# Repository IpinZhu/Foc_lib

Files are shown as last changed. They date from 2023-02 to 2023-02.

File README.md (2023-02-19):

## 重启Foc项目(Great FOC Restart Project)

### 1.概论和目标

基于STM32系列芯片的HAL库Foc代码库，和配套硬件电路

1.采用基本的Foc算法,支持开环和闭环，提供标准API接口

2.自动PID校准功能（待定）

3.支持有感电机和无感电机

4.引入龙伯格观测器，实现无感滤波

5.Rtos程序，可加入用户自定APP

6.宽电压输入范围和输出大电流



### 2.硬件

1.使用DRV8301作为三路逆变器的控制芯片，将功率模块和控制模块区分成上下半区部分。

2.主控采用STM32F405RGT6

3.提供一个外部SPI,一个CAN总线和一个复用的TypeC口，可同时将设备进行串口通信和作为USB设备使用

##### DRV8301

自带一个TPS54160Buck芯片，可以对6-60v输入进行降压处理，由于实际使用不超过25V，因此选取6-35V的输入范围，输出5V电压

### 3.软件

##### 1.foc.c和foc.h

主要由基本foc算法变换，参照st电机库，使用Q1.15形式（注.无法使用Q1.32格式，计算时会溢出）

##### SVPWM：

##### 定时器配置

分频系数为1-1=0

计数模式为中心计数模式，作用频率为10k，为168M/10K/2

RCR设置为1

### 4.RTOS

主任务

屏幕显示任务

### 5.上位机

懒得写。。。。。。

 Foc_lib

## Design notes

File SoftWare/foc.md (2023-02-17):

## 重启Foc项目(Great FOC Restart Project)

### 1.概论

基于STM32系列芯片的HAL库Foc代码库，适用于几乎所有的STM32芯片

1.采用基本的Foc算法,支持开环和闭环，提供标准API接口

2.自动PID校准功能（待定）

3.支持有感电机和无感电机

4.引入龙伯格观测器，实现无感滤波

5.Rtos程序，可加入用户自定APP



### 2.硬件

使用DRV8301作为三路逆变器的控制芯片，将功率模块和控制模块区分成上下板部分

主控采用F405RGT6

##### DRV8301

自带一个TPS54160Buck芯片，可以对6-60v输入进行降压处理，由于实际使用不超过25V，因此选取6-35V的输入范围，输出5V电压



### 3.软件

##### 1.foc.c和foc.h

主要由基本foc算法变换，参照st电机库，使用Q1.15形式（注.无法使用Q1.32格式，计算时会溢出）



使用到的结构体：

```c
typedef struct
{
    int16_t alpha;
    int16_t beta;
} alphabeta_t;

typedef struct
{
    int16_t a;
    int16_t b;
} ab_t;

typedef struct
{
    int16_t q;
    int16_t d;
} qd_t;

typedef struct
{
    int16_t hCos;
    int16_t hSin;
} Trig_Components;
```

##### 2.svpwm.c和svpwm.h

##### 七段式定时器控制：







分频系数为1-1=0

计数模式为中心计数模式，作用频率为10k，为168M/10K/2

RCR设置为1

### 4.RTOS

主任务

屏幕显示任务

### 5.上位机

懒得写。。。。。。

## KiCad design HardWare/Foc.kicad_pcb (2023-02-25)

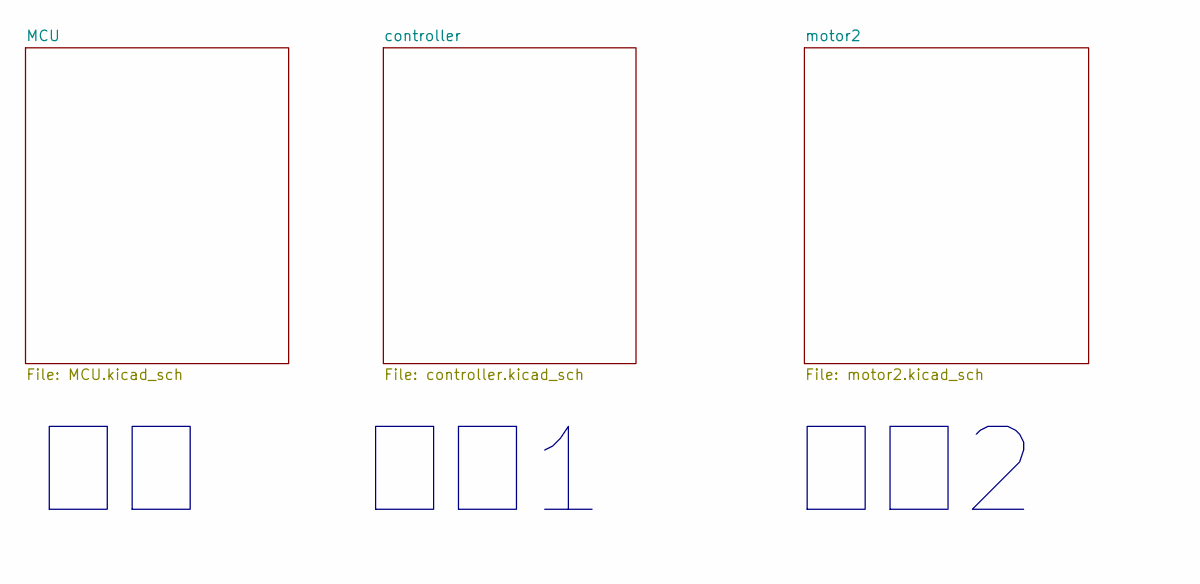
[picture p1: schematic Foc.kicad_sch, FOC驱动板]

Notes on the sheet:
电机2
电机1

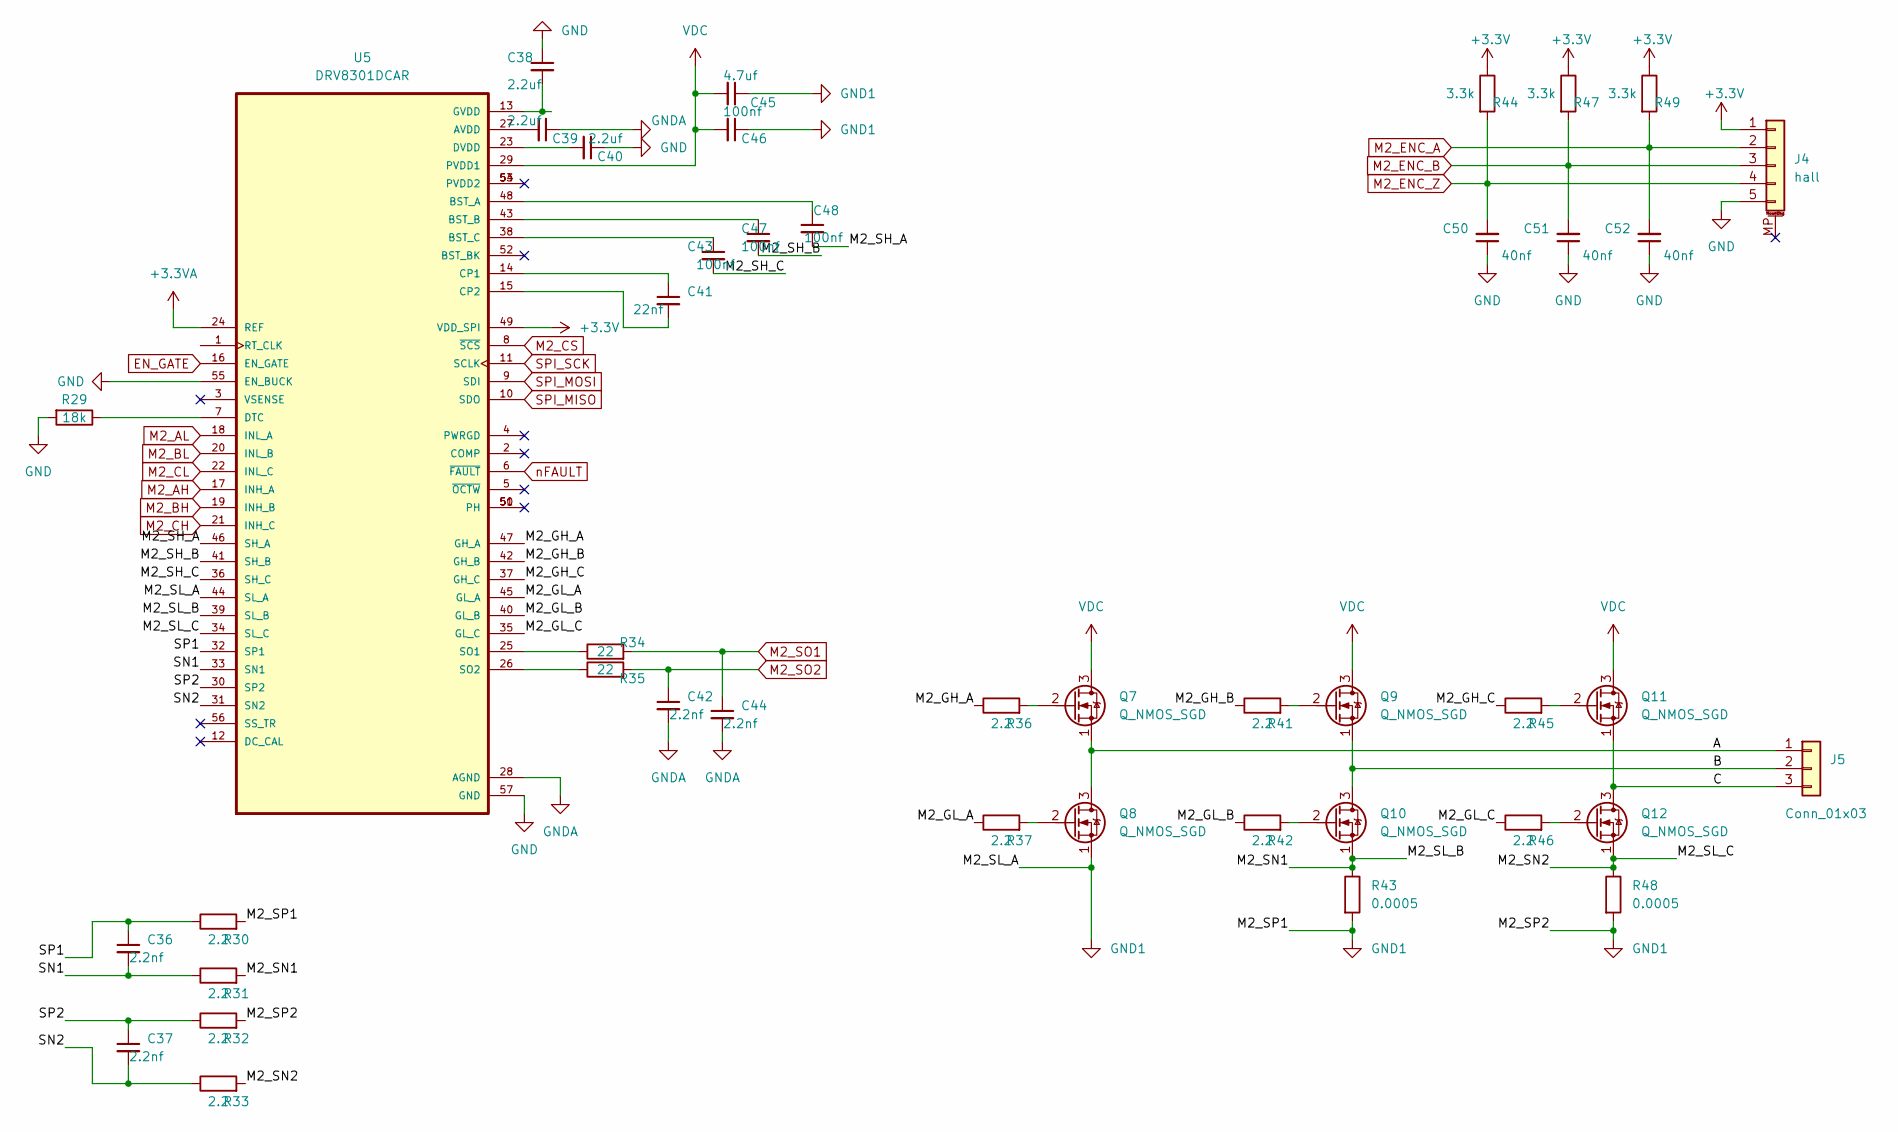
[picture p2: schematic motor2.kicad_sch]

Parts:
C36, C37, C42, C44: 2.2nf; C_0603_1608Metric
C38, C39, C40: 2.2uf; C_0603_1608Metric
C41: 22nf; C_0603_1608Metric
C43, C46, C47, C48: 100nf; C_0603_1608Metric
C45: 4.7uf; C_0603_1608Metric
C50, C51, C52: 40nf; C_0603_1608Metric
J4: hall; M1010RS-05P
J5: Conn_01x03; MR30-M
Q7, Q8, Q9, Q10, Q11, Q12: Q_NMOS_SGD; VSONP-8-1EP_5x6_P1.27mm
R29: 18k; R_0603_1608Metric
R30, R31, R32, R33, R36, R37, R41, R42, R45, R46: 2.2; R_0603_1608Metric
R34, R35: 22; R_0603_1608Metric
R43, R48: 0.0005; R_2512_6332Metric
R44, R47, R49: 3.3k; R_0603_1608Metric
U5: DRV8301DCAR; HTSSOP-56-1EP_6.1x14mm_P0.5mm_EP3.61x6.35mm; PARTREV F

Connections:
+3.3V: J4.1, R44.1, R47.1, R49.1, U5.49 (VDD_SPI); also elsewhere on the board
+3.3VA: U5.24 (REF); also elsewhere on the board
/motor2/A: J5.1, Q7.1 (S), Q8.3 (D)
/motor2/B: J5.2, Q9.1 (S), Q10.3 (D)
/motor2/C: J5.3, Q11.1 (S), Q12.3 (D)
/motor2/M2_GH_A: R36.1, U5.47 (GH_A)
/motor2/M2_GH_B: R41.1, U5.42 (GH_B)
/motor2/M2_GH_C: R45.1, U5.37 (GH_C)
/motor2/M2_GL_A: R37.1, U5.45 (GL_A)
/motor2/M2_GL_B: R42.1, U5.40 (GL_B)
/motor2/M2_GL_C: R46.1, U5.35 (GL_C)
/motor2/M2_SH_A: C48.2, U5.46 (SH_A)
/motor2/M2_SH_B: C47.2, U5.41 (SH_B)
/motor2/M2_SH_C: C43.2, U5.36 (SH_C)
/motor2/M2_SL_B: Q10.1 (S), R31.2, R43.1, U5.39 (SL_B)
/motor2/M2_SL_C: Q12.1 (S), R33.2, R48.1, U5.34 (SL_C)
/motor2/SN1: C36.2, R31.1, U5.33 (SN1)
/motor2/SN2: C37.2, R33.1, U5.31 (SN2)
/motor2/SP1: C36.1, R30.1, U5.32 (SP1)
/motor2/SP2: C37.1, R32.1, U5.30 (SP2)
EN_GATE: U5.16 (EN_GATE); also elsewhere on the board
GND: C38.1, C39.1, C40.1, C42.2, C44.2, C50.1, C51.1, C52.1, J4.5, R29.2, U5.28 (AGND), U5.55 (EN_BUCK), U5.57 (GND); also elsewhere on the board
GND1: C45.1, C46.1, Q8.1 (S), R30.2, R32.2, R43.2, R48.2, U5.44 (SL_A); also elsewhere on the board
M2_AH: U5.17 (INH_A); also elsewhere on the board
M2_AL: U5.18 (INL_A); also elsewhere on the board
M2_BH: U5.19 (INH_B); also elsewhere on the board
M2_BL: U5.20 (INL_B); also elsewhere on the board
M2_CH: U5.21 (INH_C); also elsewhere on the board
M2_CL: U5.22 (INL_C); also elsewhere on the board
M2_CS: U5.8 (~SCS); also elsewhere on the board
M2_ENC_A: C52.2, J4.2, R49.2; also elsewhere on the board
M2_ENC_B: C51.2, J4.3, R47.2; also elsewhere on the board
M2_ENC_Z: C50.2, J4.4, R44.2; also elsewhere on the board
M2_SO1: C44.1, R34.2; also elsewhere on the board
M2_SO2: C42.1, R35.2; also elsewhere on the board
unnamed: C38.2, U5.13 (GVDD)
unnamed: C39.2, U5.27 (AVDD)
unnamed: C40.2, U5.23 (DVDD)
unnamed: C41.1, U5.14 (CP1)
unnamed: C41.2, U5.15 (CP2)
unnamed: C43.1, U5.38 (BST_C)
unnamed: C47.1, U5.43 (BST_B)
unnamed: C48.1, U5.48 (BST_A)
unnamed: Q7.2 (G), R36.2
unnamed: Q8.2 (G), R37.2
unnamed: Q9.2 (G), R41.2
unnamed: Q10.2 (G), R42.2
unnamed: Q11.2 (G), R45.2
unnamed: Q12.2 (G), R46.2
unnamed: R29.1, U5.7 (DTC)
unnamed: R34.1, U5.25 (SO1)
unnamed: R35.1, U5.26 (SO2)
SPI_MISO: U5.10 (SDO); also elsewhere on the board
SPI_MOSI: U5.9 (SDI); also elsewhere on the board
SPI_SCK: U5.11 (SCLK); also elsewhere on the board
VDC: C45.2, C46.2, Q7.3 (D), Q9.3 (D), Q11.3 (D), U5.29 (PVDD1); also elsewhere on the board
nFAULT: U5.6 (~FAULT); also elsewhere on the board

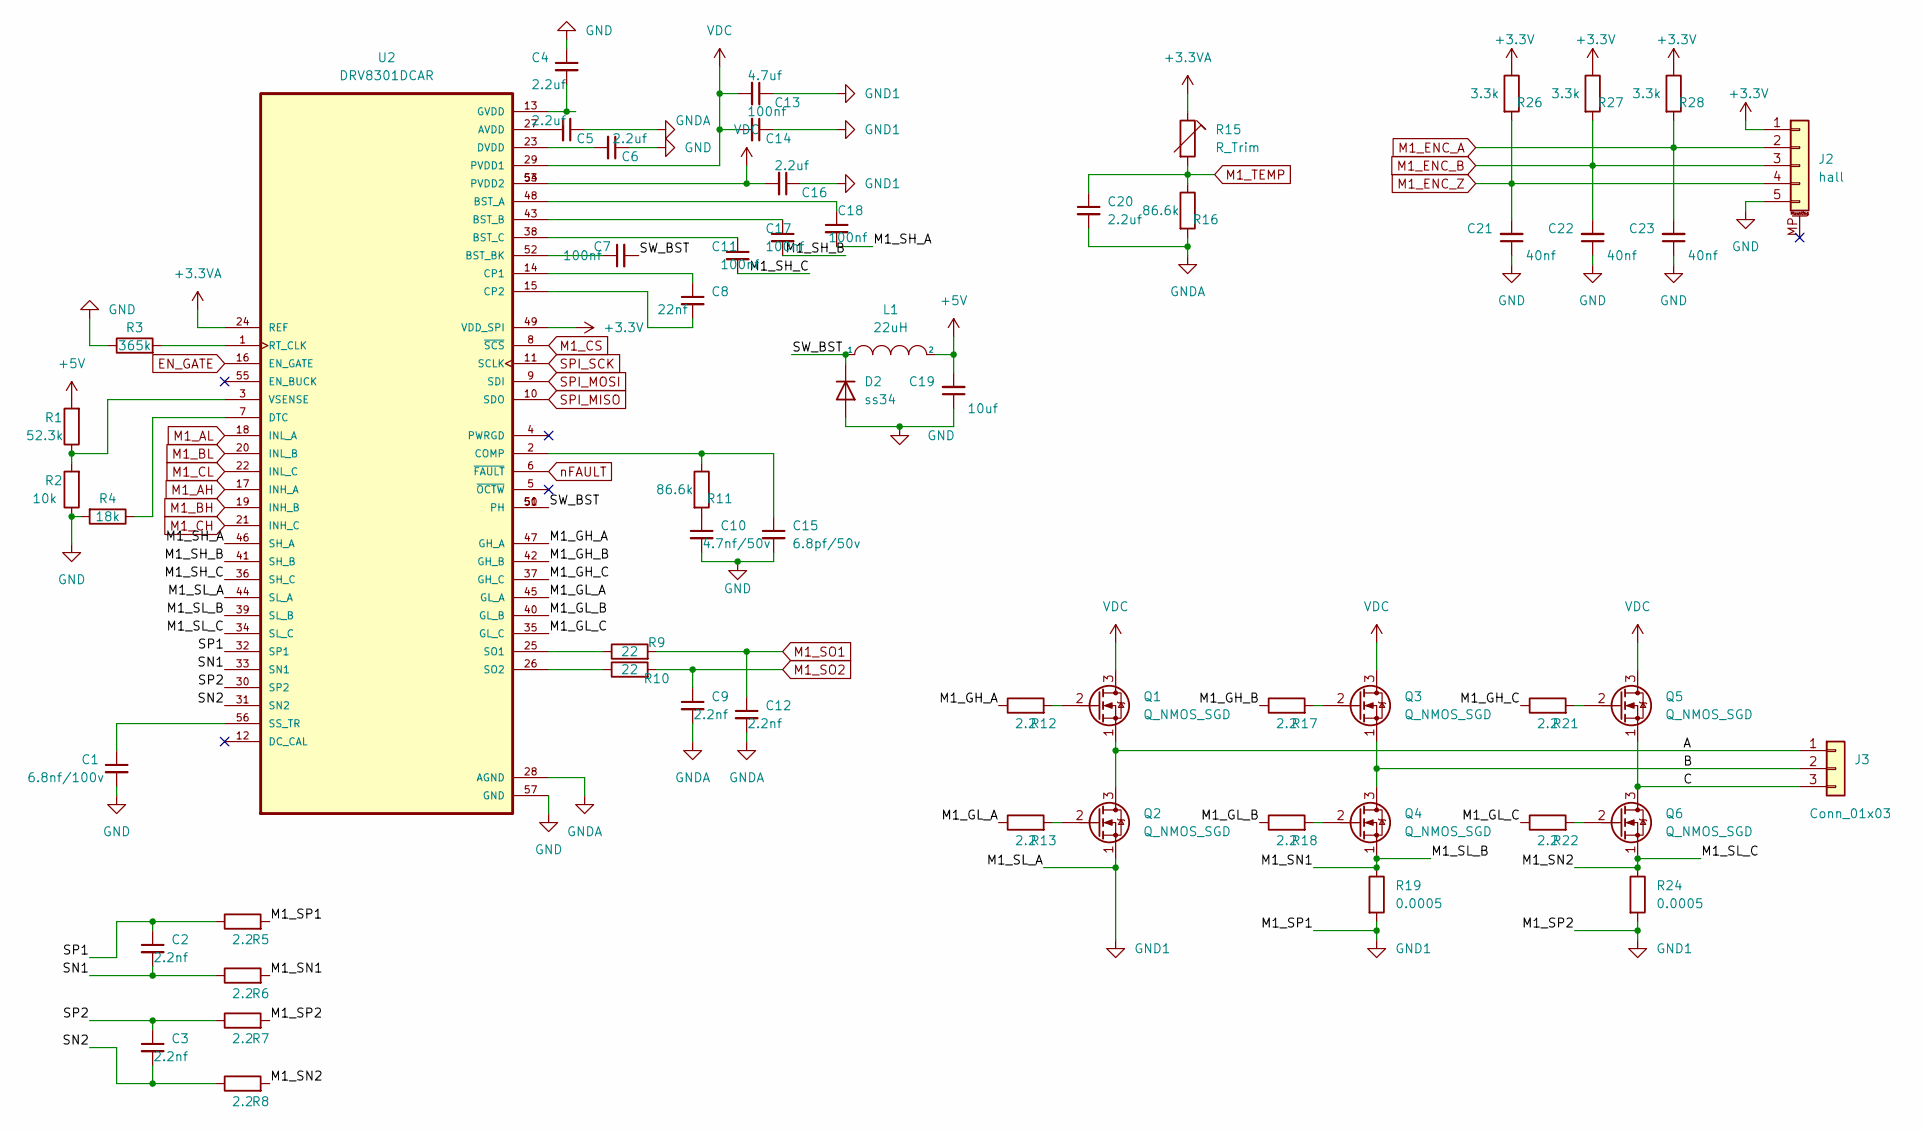
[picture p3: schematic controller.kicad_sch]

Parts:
C1: 6.8nf/100v; C_0603_1608Metric
C2, C3, C9, C12: 2.2nf; C_0603_1608Metric
C4, C5, C6, C16, C20: 2.2uf; C_0603_1608Metric
C7, C11, C14, C17, C18: 100nf; C_0603_1608Metric
C8: 22nf; C_0603_1608Metric
C10: 4.7nf/50v; C_0603_1608Metric
C13: 4.7uf; C_0603_1608Metric
C15: 6.8pf/50v; C_0603_1608Metric
C19: 10uf; C_1210_3225Metric
C21, C22, C23: 40nf; C_0603_1608Metric
D2: ss34; D_SMA
J2: hall; M1010RS-05P
J3: Conn_01x03; MR30-M
L1: 22uH; L_Abracon_ASPI-0630LR
Q1, Q2, Q3, Q4, Q5, Q6: Q_NMOS_SGD; VSONP-8-1EP_5x6_P1.27mm
R1: 52.3k; R_0603_1608Metric
R2: 10k; R_0603_1608Metric
R3: 365k; R_0603_1608Metric
R4: 18k; R_0603_1608Metric
R5, R6, R7, R8, R12, R13, R17, R18, R21, R22: 2.2; R_0603_1608Metric
R9, R10: 22; R_0603_1608Metric
R11, R16: 86.6k; R_0603_1608Metric
R15: R_Trim; R_0603_1608Metric
R19, R24: 0.0005; R_2512_6332Metric
R26, R27, R28: 3.3k; R_0603_1608Metric
U2: DRV8301DCAR; HTSSOP-56-1EP_6.1x14mm_P0.5mm_EP3.61x6.35mm; PARTREV F

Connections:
+3.3V: J2.1, R26.1, R27.1, R28.1, U2.49 (VDD_SPI); also elsewhere on the board
+3.3VA: R15.1, U2.24 (REF); also elsewhere on the board
+5V: C19.2, L1.2, R1.2; also elsewhere on the board
/controller/A: J3.1, Q1.1 (S), Q2.3 (D)
/controller/B: J3.2, Q3.1 (S), Q4.3 (D)
/controller/C: J3.3, Q5.1 (S), Q6.3 (D)
/controller/M1_GH_A: R12.1, U2.47 (GH_A)
/controller/M1_GH_B: R17.1, U2.42 (GH_B)
/controller/M1_GH_C: R21.1, U2.37 (GH_C)
/controller/M1_GL_A: R13.1, U2.45 (GL_A)
/controller/M1_GL_B: R18.1, U2.40 (GL_B)
/controller/M1_GL_C: R22.1, U2.35 (GL_C)
/controller/M1_SH_A: C18.2, U2.46 (SH_A)
/controller/M1_SH_B: C17.2, U2.41 (SH_B)
/controller/M1_SH_C: C11.2, U2.36 (SH_C)
/controller/M1_SL_B: Q4.1 (S), R6.2, R19.1, U2.39 (SL_B)
/controller/M1_SL_C: Q6.1 (S), R8.2, R24.1, U2.34 (SL_C)
/controller/SN1: C2.2, R6.1, U2.33 (SN1)
/controller/SN2: C3.2, R8.1, U2.31 (SN2)
/controller/SP1: C2.1, R5.1, U2.32 (SP1)
/controller/SP2: C3.1, R7.1, U2.30 (SP2)
/controller/SW_BST: C7.2, D2.2 (K), L1.1, U2.50 (PH), U2.51 (PH)
EN_GATE: U2.16 (EN_GATE); also elsewhere on the board
GND: C1.2, C4.1, C5.1, C6.1, C9.2, C10.2, C12.2, C15.2, C19.1, C20.2, C21.1, C22.1, C23.1, D2.1 (A), J2.5, R2.1, R3.1, R4.2, R16.2, U2.28 (AGND), U2.57 (GND); also elsewhere on the board
GND1: C13.1, C14.1, C16.1, Q2.1 (S), R5.2, R7.2, R19.2, R24.2, U2.44 (SL_A); also elsewhere on the board
M1_AH: U2.17 (INH_A); also elsewhere on the board
M1_AL: U2.18 (INL_A); also elsewhere on the board
M1_BH: U2.19 (INH_B); also elsewhere on the board
M1_BL: U2.20 (INL_B); also elsewhere on the board
M1_CH: U2.21 (INH_C); also elsewhere on the board
M1_CL: U2.22 (INL_C); also elsewhere on the board
M1_CS: U2.8 (~SCS); also elsewhere on the board
M1_ENC_A: C23.2, J2.2, R28.2; also elsewhere on the board
M1_ENC_B: C22.2, J2.3, R27.2; also elsewhere on the board
M1_ENC_Z: C21.2, J2.4, R26.2; also elsewhere on the board
M1_SO1: C12.1, R9.2; also elsewhere on the board
M1_SO2: C9.1, R10.2; also elsewhere on the board
M1_TEMP: C20.1, R15.2, R16.1; also elsewhere on the board
unnamed: C1.1, U2.56 (SS_TR)
unnamed: C4.2, U2.13 (GVDD)
unnamed: C5.2, U2.27 (AVDD)
unnamed: C6.2, U2.23 (DVDD)
unnamed: C7.1, U2.52 (BST_BK)
unnamed: C8.1, U2.14 (CP1)
unnamed: C8.2, U2.15 (CP2)
unnamed: C10.1, R11.2
unnamed: C11.1, U2.38 (BST_C)
unnamed: C15.1, R11.1, U2.2 (COMP)
unnamed: C17.1, U2.43 (BST_B)
unnamed: C18.1, U2.48 (BST_A)
unnamed: Q1.2 (G), R12.2
unnamed: Q2.2 (G), R13.2
unnamed: Q3.2 (G), R17.2
unnamed: Q4.2 (G), R18.2
unnamed: Q5.2 (G), R21.2
unnamed: Q6.2 (G), R22.2
unnamed: R1.1, R2.2, U2.3 (VSENSE)
unnamed: R3.2, U2.1 (RT_CLK)
unnamed: R4.1, U2.7 (DTC)
unnamed: R9.1, U2.25 (SO1)
unnamed: R10.1, U2.26 (SO2)
SPI_MISO: U2.10 (SDO); also elsewhere on the board
SPI_MOSI: U2.9 (SDI); also elsewhere on the board
SPI_SCK: U2.11 (SCLK); also elsewhere on the board
VDC: C13.2, C14.2, C16.2, Q1.3 (D), Q3.3 (D), Q5.3 (D), U2.29 (PVDD1), U2.53 (PVDD2), U2.54 (PVDD2); also elsewhere on the board
nFAULT: U2.6 (~FAULT); also elsewhere on the board

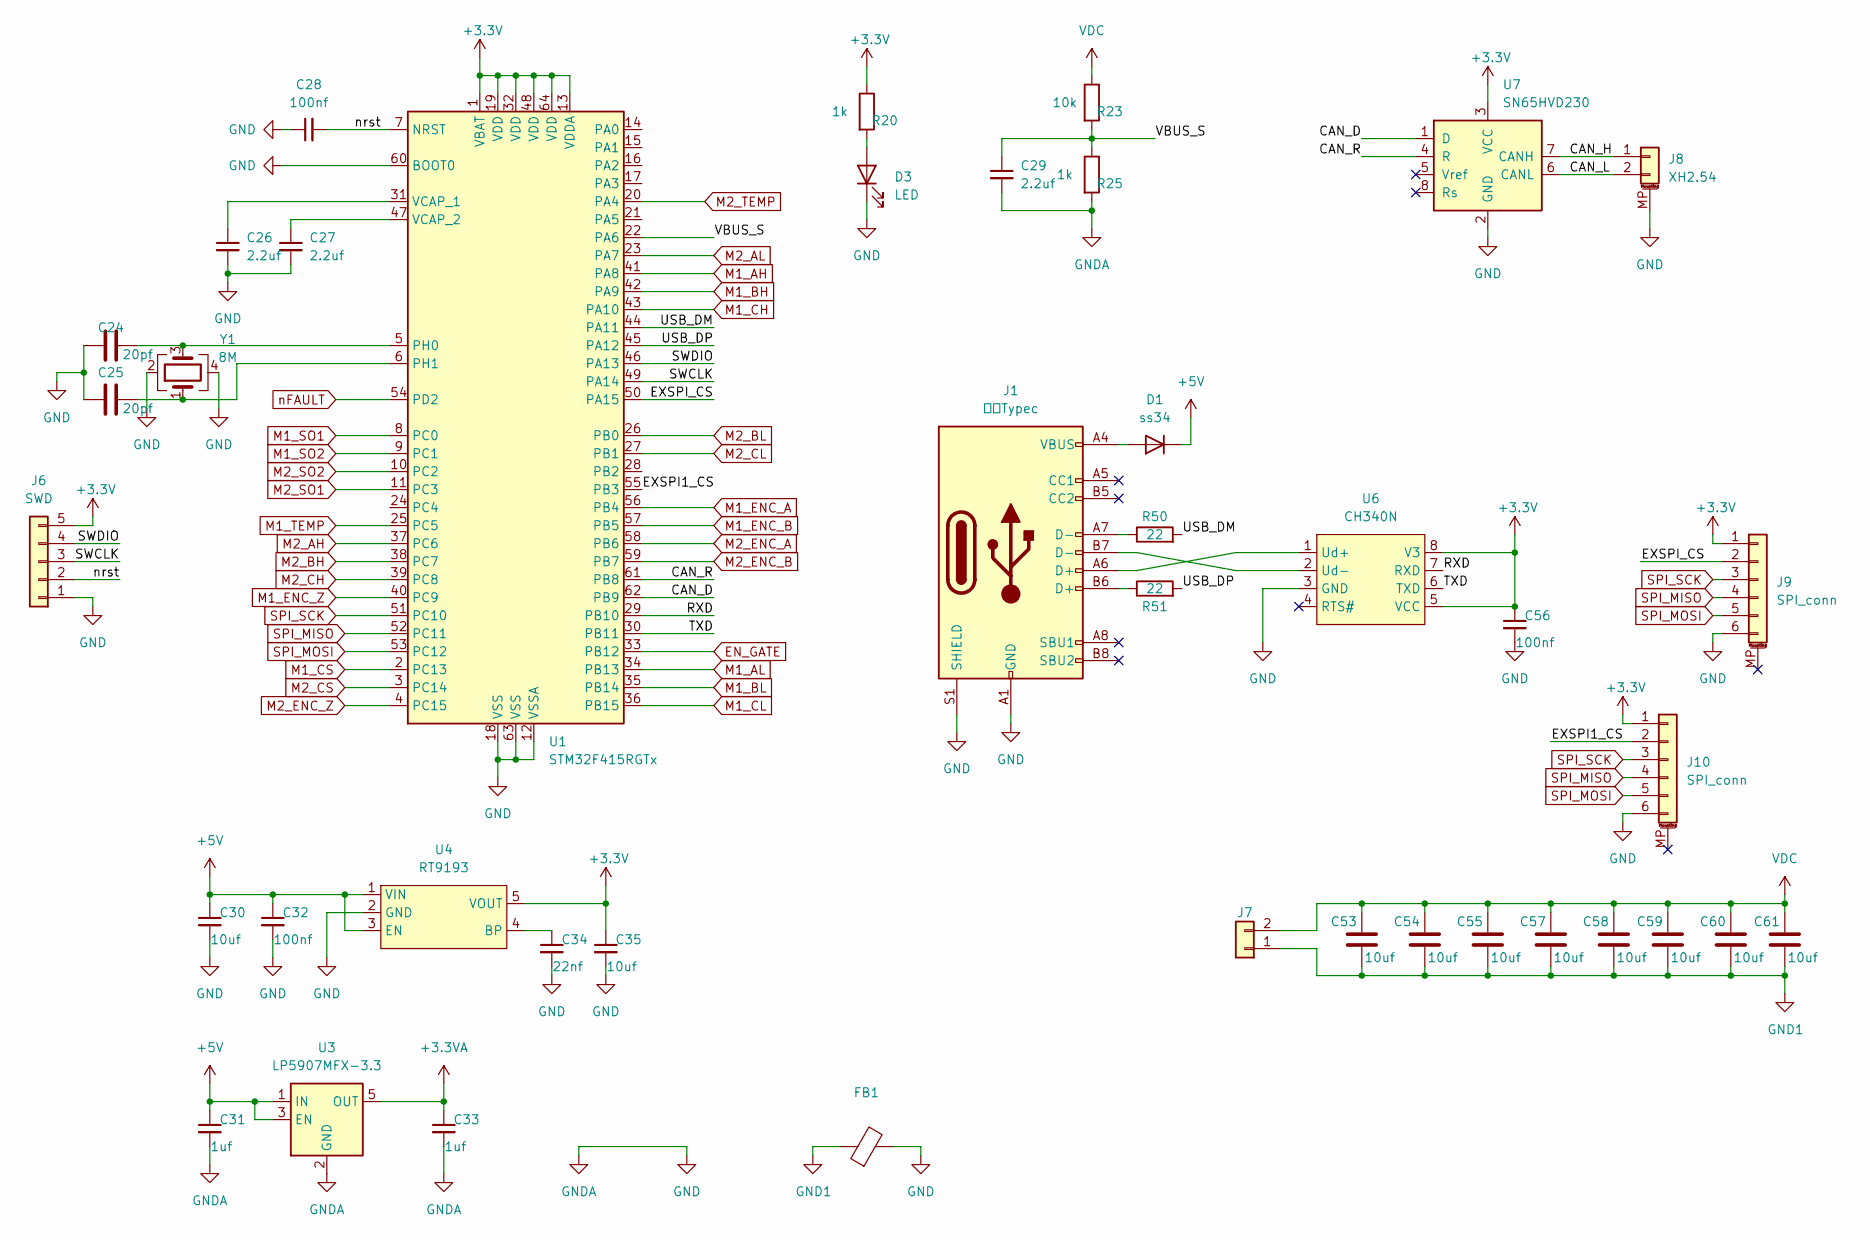
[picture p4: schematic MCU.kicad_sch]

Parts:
C24, C25: 20pf; C_0603_1608Metric
C26, C27, C29: 2.2uf; C_0603_1608Metric
C28, C32, C56: 100nf; C_0603_1608Metric
C30, C35: 10uf; C_0603_1608Metric
C31, C33: 1uf; C_0603_1608Metric
C34: 22nf; C_0603_1608Metric
C53, C54, C55, C57, C58, C59, C60, C61: 10uf; C_1210_3225Metric
D1: ss34; D_SMA
D3: LED; D_0805_2012Metric
FB1: FerriteBead; L_0805_2012Metric
J1: 复用Typec; USB_C_Receptacle_HRO_TYPE-C-31-M-12
J6: SWD; PinSocket_1x05_P2.54mm_Vertical
J7: inp; XT30U-M
J8: XH2.54; Molex_CLIK-Mate_502443-0270_1x02-1MP_P2.00mm_Vertical
J9, J10: SPI_conn; M1010RS-06P
R20, R25: 1k; R_0603_1608Metric
R23: 10k; R_0603_1608Metric
R50, R51: 22; R_0603_1608Metric
U1: STM32F415RGTx; LQFP-64_10x10mm_P0.5mm
U3: LP5907MFX-3.3; SOT-23-5
U4: RT9193; SOT-23-5
U6: CH340N; SOP-8_3.9x4.9mm_P1.27mm
U7: SN65HVD230; SOIC-8_3.9x4.9mm_P1.27mm
Y1: 8M; Crystal_SMD_3225-4Pin_3.2x2.5mm

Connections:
+3.3V: C35.1, C56.1, J6.5, J9.1, J10.1, R20.1, U1.1 (VBAT), U1.13 (VDDA), U1.19 (VDD), U1.32 (VDD), U1.48 (VDD), U1.64 (VDD), U4.5 (VOUT), U6.5 (VCC), U6.8 (V3), U7.3 (VCC); also elsewhere on the board
+3.3VA: C33.1, U3.5 (OUT); also elsewhere on the board
+5V: C30.1, C31.1, C32.1, D1.2 (K), U3.1 (IN), U3.3 (EN), U4.1 (VIN), U4.3 (EN); also elsewhere on the board
/MCU/CAN_D: U1.62 (PB9), U7.1 (D)
/MCU/CAN_H: J8.1, U7.7 (CANH)
/MCU/CAN_L: J8.2, U7.6 (CANL)
/MCU/CAN_R: U1.61 (PB8), U7.4 (R)
/MCU/EXSPI1_CS: J10.2, U1.55 (PB3)
/MCU/EXSPI_CS: J9.2, U1.50 (PA15)
/MCU/RXD: U1.29 (PB10), U6.7 (RXD)
/MCU/SWCLK: J6.3, U1.49 (PA14)
/MCU/SWDIO: J6.4, U1.46 (PA13)
/MCU/TXD: U1.30 (PB11), U6.6 (TXD)
/MCU/USB_DM: R50.2, U1.44 (PA11)
/MCU/USB_DP: R51.2, U1.45 (PA12)
/MCU/VBUS_S: C29.1, R23.2, R25.1, U1.22 (PA6)
/MCU/nrst: C28.2, J6.2, U1.7 (NRST)
EN_GATE: U1.33 (PB12); also elsewhere on the board
GND: C24.2, C25.2, C26.2, C27.2, C28.1, C29.2, C30.2, C31.2, C32.2, C33.2, C34.2, C35.2, C56.2, D3.1 (K), FB1.2, J1.A1 (GND), J1.A12 (GND), J1.B1 (GND), J1.B12 (GND), J1.S1 (SHIELD), J6.1, J8.MP (MountPin), J9.6, J10.6, R25.2, U1.12 (VSSA), U1.18 (VSS), U1.60 (BOOT0), U1.63 (VSS), U3.2 (GND), U4.2 (GND), U6.3 (GND), U7.2 (GND), Y1.2, Y1.4; also elsewhere on the board
GND1: C53.2, C54.2, C55.2, C57.2, C58.2, C59.2, C60.2, C61.2, FB1.1, J7.1; also elsewhere on the board
M1_AH: U1.41 (PA8); also elsewhere on the board
M1_AL: U1.34 (PB13); also elsewhere on the board
M1_BH: U1.42 (PA9); also elsewhere on the board
M1_BL: U1.35 (PB14); also elsewhere on the board
M1_CH: U1.43 (PA10); also elsewhere on the board
M1_CL: U1.36 (PB15); also elsewhere on the board
M1_CS: U1.2 (PC13); also elsewhere on the board
M1_ENC_A: U1.56 (PB4); also elsewhere on the board
M1_ENC_B: U1.57 (PB5); also elsewhere on the board
M1_ENC_Z: U1.40 (PC9); also elsewhere on the board
M1_SO1: U1.8 (PC0); also elsewhere on the board
M1_SO2: U1.9 (PC1); also elsewhere on the board
M1_TEMP: U1.25 (PC5); also elsewhere on the board
M2_AH: U1.37 (PC6); also elsewhere on the board
M2_AL: U1.23 (PA7); also elsewhere on the board
M2_BH: U1.38 (PC7); also elsewhere on the board
M2_BL: U1.26 (PB0); also elsewhere on the board
M2_CH: U1.39 (PC8); also elsewhere on the board
M2_CL: U1.27 (PB1); also elsewhere on the board
M2_CS: U1.3 (PC14); also elsewhere on the board
M2_ENC_A: U1.58 (PB6); also elsewhere on the board
M2_ENC_B: U1.59 (PB7); also elsewhere on the board
M2_ENC_Z: U1.4 (PC15); also elsewhere on the board
M2_SO1: U1.11 (PC3); also elsewhere on the board
M2_SO2: U1.10 (PC2); also elsewhere on the board
M2_TEMP: U1.20 (PA4)
unnamed: C24.1, U1.5 (PH0), Y1.3
unnamed: C25.1, U1.6 (PH1), Y1.1
unnamed: C26.1, U1.31 (VCAP_1)
unnamed: C27.1, U1.47 (VCAP_2)
unnamed: C34.1, U4.4 (BP)
unnamed: D1.1 (A), J1.A4 (VBUS), J1.A9 (VBUS), J1.B4 (VBUS), J1.B9 (VBUS)
unnamed: D3.2 (A), R20.2
unnamed: J1.A6 (D+), U6.1 (Ud+)
unnamed: J1.A7 (D-), R50.1
unnamed: J1.B6 (D+), R51.1
unnamed: J1.B7 (D-), U6.2 (Ud-)
SPI_MISO: J9.4, J10.4, U1.52 (PC11); also elsewhere on the board
SPI_MOSI: J9.5, J10.5, U1.53 (PC12); also elsewhere on the board
SPI_SCK: J9.3, J10.3, U1.51 (PC10); also elsewhere on the board
VDC: C53.1, C54.1, C55.1, C57.1, C58.1, C59.1, C60.1, C61.1, J7.2, R23.1; also elsewhere on the board
nFAULT: U1.54 (PD2); also elsewhere on the board

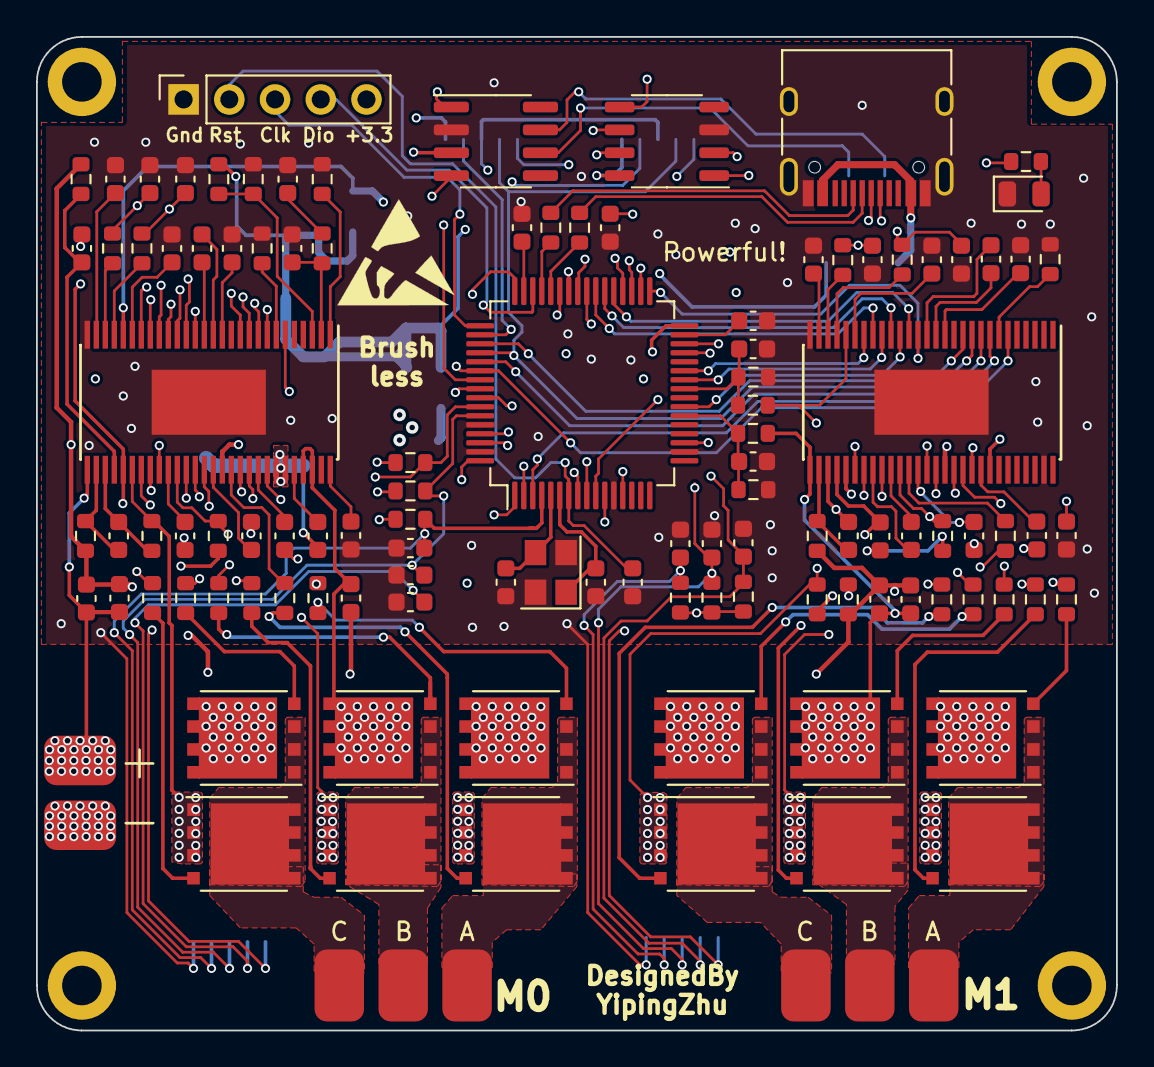
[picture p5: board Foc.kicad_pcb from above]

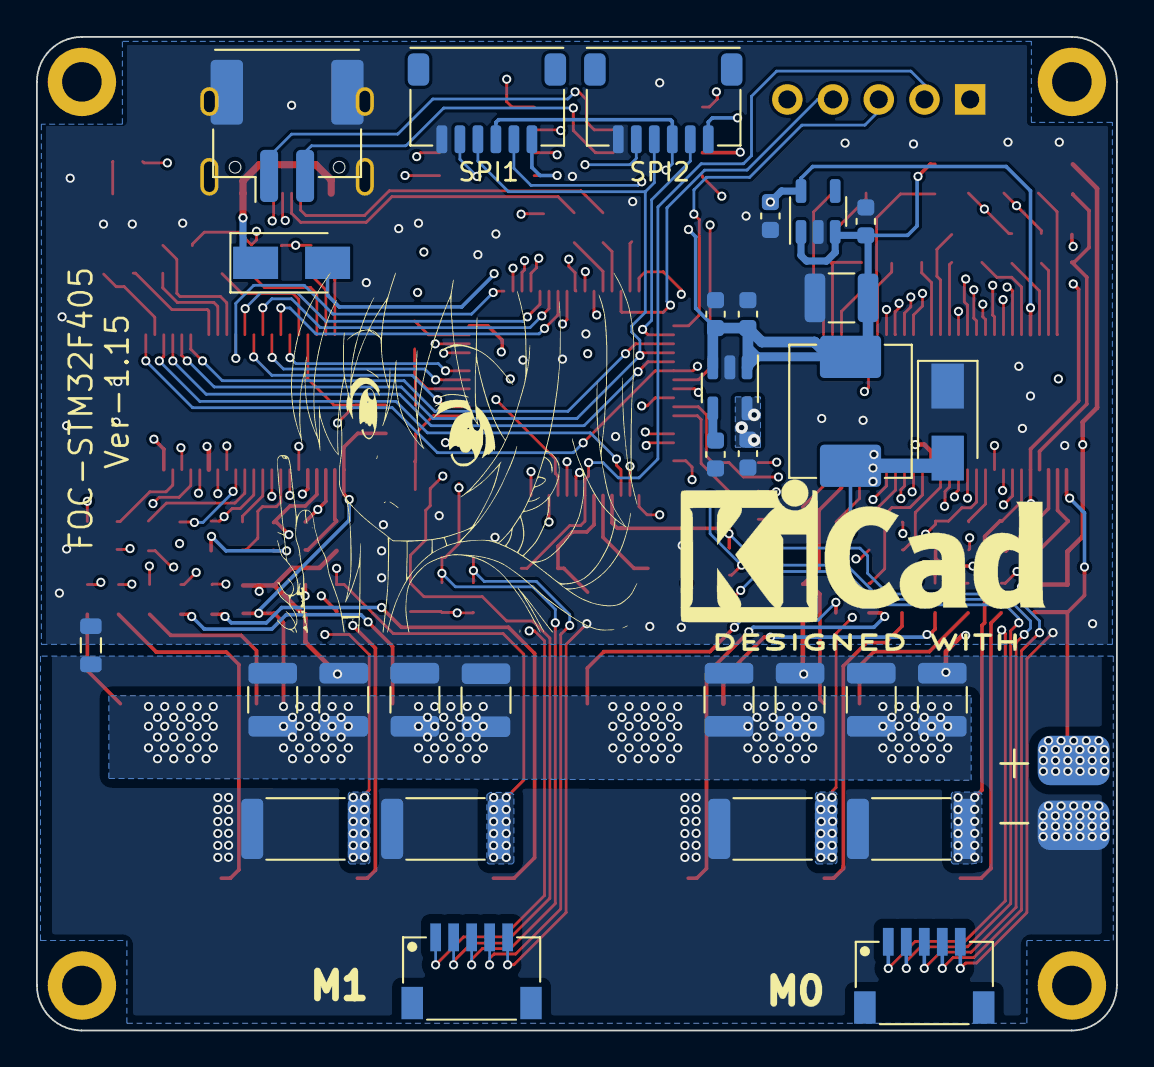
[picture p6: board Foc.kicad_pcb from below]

Board: 4 copper layers, 60.0 x 55.2 mm, 147 parts (30 on the bottom side), 138 nets.

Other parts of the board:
C156: 100nf; C_0603_1608Metric
REFA: MountingHole_2.2mm_M2_DIN965_Pad
REFB: MountingHole_2.2mm_M2_DIN965_Pad
REFC: MountingHole_2.2mm_M2_DIN965_Pad
REFD: MountingHole_2.2mm_M2_DIN965_Pad

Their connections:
+3.3V: C156.1; also elsewhere on the board
GND: C156.2; also elsewhere on the board

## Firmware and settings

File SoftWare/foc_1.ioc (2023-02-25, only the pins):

Mcu.UserName=STM32F405RGTx
PA10.Signal=S_TIM1_CH3
PA11.Signal=USB_OTG_FS_DM
PA12.Signal=USB_OTG_FS_DP
PA13.Signal=SYS_JTMS-SWDIO
PA14.Signal=SYS_JTCK-SWCLK
PA15.GPIO_Label=EXSPI_CS
PA15.Signal=GPIO_Output
PA4.GPIO_Label=M1_TEMP
PA4.Signal=ADCx_IN4
PA6.GPIO_Label=VBUS_S
PA6.Signal=ADCx_IN6
PA7.Signal=TIM8_CH1N
PA8.Signal=S_TIM1_CH1
PA9.Signal=S_TIM1_CH2
PB0.Signal=TIM8_CH2N
PB1.Signal=TIM8_CH3N
PB10.Signal=USART3_TX
PB11.Signal=USART3_RX
PB12.GPIO_Label=EN_GATE
PB12.Signal=GPIO_Output
PB13.Signal=TIM1_CH1N
PB14.Signal=TIM1_CH2N
PB15.Signal=TIM1_CH3N
PB4.GPIO_Label=M0_ENC_A
PB4.Signal=GPIO_Input
PB5.GPIO_Label=M0_ENC_B
PB5.Signal=GPIO_Input
PB6.GPIO_Label=M1_ENC_A
PB6.Signal=GPIO_Input
PB7.GPIO_Label=M1_ENC_B
PB7.Signal=GPIO_Input
PB8.Signal=CAN1_RX
PB9.Signal=CAN1_TX
PC0.GPIO_Label=M0_SO1
PC0.Signal=ADCx_IN10
PC1.GPIO_Label=M0_SO2
PC1.Signal=ADCx_IN11
PC10.Signal=SPI3_SCK
PC11.Signal=SPI3_MISO
PC12.Signal=SPI3_MOSI
PC13-ANTI_TAMP.GPIO_Label=M0_CS
PC13-ANTI_TAMP.Signal=GPIO_Output
PC14-OSC32_IN.GPIO_Label=M1_CS
PC14-OSC32_IN.Signal=GPIO_Output
PC15-OSC32_OUT.GPIO_Label=M1_ENC_Z
PC15-OSC32_OUT.Signal=GPIO_Input
PC2.GPIO_Label=M1_SO2
PC2.Signal=ADCx_IN12
PC3.GPIO_Label=M1_SO1
PC3.Signal=ADCx_IN13
PC5.GPIO_Label=M0_TEMP
PC5.Signal=ADCx_IN15
PC6.Signal=S_TIM8_CH1
PC7.Signal=S_TIM8_CH2
PC8.Signal=S_TIM8_CH3
PC9.GPIO_Label=M1_ENC_Z
PC9.Signal=GPIO_Input
PD2.GPIO_Label=nFAULT
PD2.Signal=GPIO_Input
PH0-OSC_IN.Signal=RCC_OSC_IN
PH1-OSC_OUT.Signal=RCC_OSC_OUT

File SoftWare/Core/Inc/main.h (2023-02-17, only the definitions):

#define M0_CS_Pin GPIO_PIN_13
#define M0_CS_GPIO_Port GPIOC
#define M1_CS_Pin GPIO_PIN_14
#define M1_CS_GPIO_Port GPIOC
#define M1_ENC_Z_Pin GPIO_PIN_15
#define M1_ENC_Z_GPIO_Port GPIOC
#define M0_SO1_Pin GPIO_PIN_0
#define M0_SO1_GPIO_Port GPIOC
#define M0_SO2_Pin GPIO_PIN_1
#define M0_SO2_GPIO_Port GPIOC
#define M1_SO2_Pin GPIO_PIN_2
#define M1_SO2_GPIO_Port GPIOC
#define M1_SO1_Pin GPIO_PIN_3
#define M1_SO1_GPIO_Port GPIOC
#define M1_TEMP_Pin GPIO_PIN_4
#define M1_TEMP_GPIO_Port GPIOA
#define VBUS_S_Pin GPIO_PIN_6
#define VBUS_S_GPIO_Port GPIOA
#define M0_TEMP_Pin GPIO_PIN_5
#define M0_TEMP_GPIO_Port GPIOC
#define EN_GATE_Pin GPIO_PIN_12
#define EN_GATE_GPIO_Port GPIOB
#define M1_ENC_ZC9_Pin GPIO_PIN_9
#define M1_ENC_ZC9_GPIO_Port GPIOC
#define nFAULT_Pin GPIO_PIN_2
#define nFAULT_GPIO_Port GPIOD
#define M0_ENC_A_Pin GPIO_PIN_4
#define M0_ENC_A_GPIO_Port GPIOB
#define M0_ENC_B_Pin GPIO_PIN_5
#define M0_ENC_B_GPIO_Port GPIOB
#define M1_ENC_A_Pin GPIO_PIN_6
#define M1_ENC_A_GPIO_Port GPIOB
#define M1_ENC_B_Pin GPIO_PIN_7
#define M1_ENC_B_GPIO_Port GPIOB

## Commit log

2023-02-17 First push
    [Foc.kicad_pcb, Foc.kicad_sch, MCU.kicad_sch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]
2023-02-17 Add PCB
    [Foc.kicad_pcb, Foc.kicad_sch, MCU.kicad_sch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]
2023-02-18 Add Rules
    [Foc.kicad_pcb, Foc.kicad_sch, MCU.kicad_sch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]
2023-02-18 增加一些功率器件有关的pcb电路
    [Foc.kicad_pcb, Foc.kicad_sch, controller.kicad_sch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]
2023-02-18 修改硬件电路
    [Foc.kicad_pcb]
2023-02-18 修改README
2023-02-19 修改一些BUG
    [Foc.kicad_pcb, Foc.kicad_sch, MCU.kicad_sch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]
2023-02-19 更新一些信号电源
    [Foc.kicad_pcb, Foc.kicad_sch, MCU.kicad_sch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]
2023-02-19 日常更新
    [Foc.kicad_pcb, Foc.kicad_sch, MCU.kicad_sch]
2023-02-19 改bug
2023-02-20 修改pcb中信号部分
    [Foc.kicad_pcb, Foc.kicad_sch, MCU.kicad_sch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]
2023-02-20 画一部分的信号
    [Foc.kicad_pcb, motor2.kicad_sch]
2023-02-22 完成PCB
    [Foc.kicad_pcb, Foc.kicad_sch, MCU.kicad_sch]
2023-02-23 PCB打样
    [Foc.kicad_pcb]
2023-02-25 添加PI控制器
    [Foc.kicad_pcb]

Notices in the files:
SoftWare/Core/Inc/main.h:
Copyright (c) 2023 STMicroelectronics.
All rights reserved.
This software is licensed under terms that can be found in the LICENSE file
